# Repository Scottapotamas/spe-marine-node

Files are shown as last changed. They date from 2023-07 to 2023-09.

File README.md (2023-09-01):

# Underwater Sensor Node with Single Pair Ethernet
Prototype project to build a underwater sensor node, powered by and communicating with the surface via Single Pair Ethernet (10BASE-T1L + 802.3cg Type E Class 10-12).

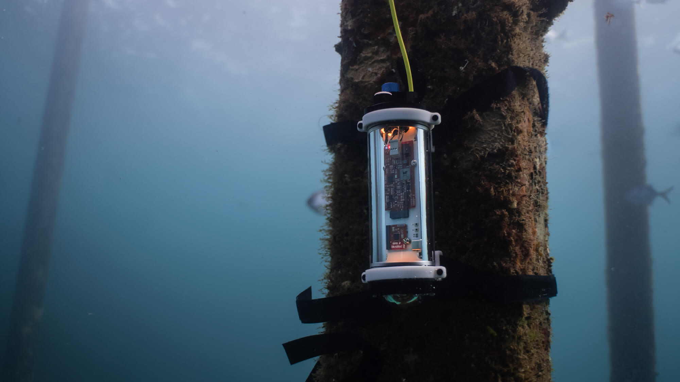
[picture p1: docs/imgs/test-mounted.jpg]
test-mounted


A more detailed write-up can be [read on Electric UI's blog](https://electricui.com/blog/spe-sensor-node).

# Mechanical

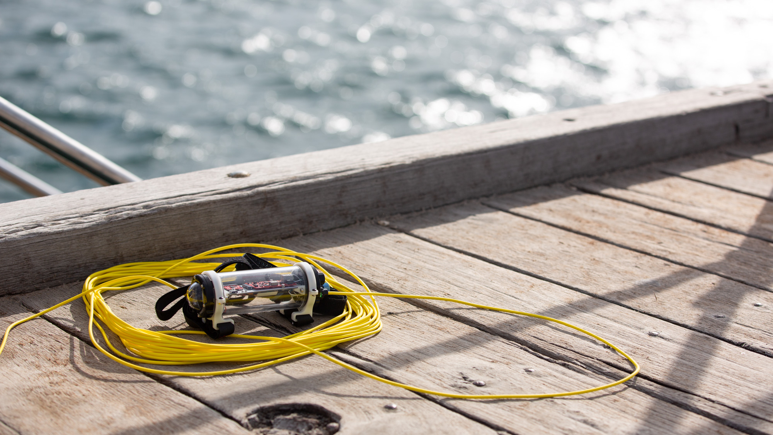
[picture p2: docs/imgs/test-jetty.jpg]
test-jetty


## Housing

The body of the sensor node is a 2″ acrylic tube (*~58mm OD*), with a pair of aluminium end-caps. This provides a working volume constrained by the 50 mm internal diameter and ~118 mm maximum gap between caps.

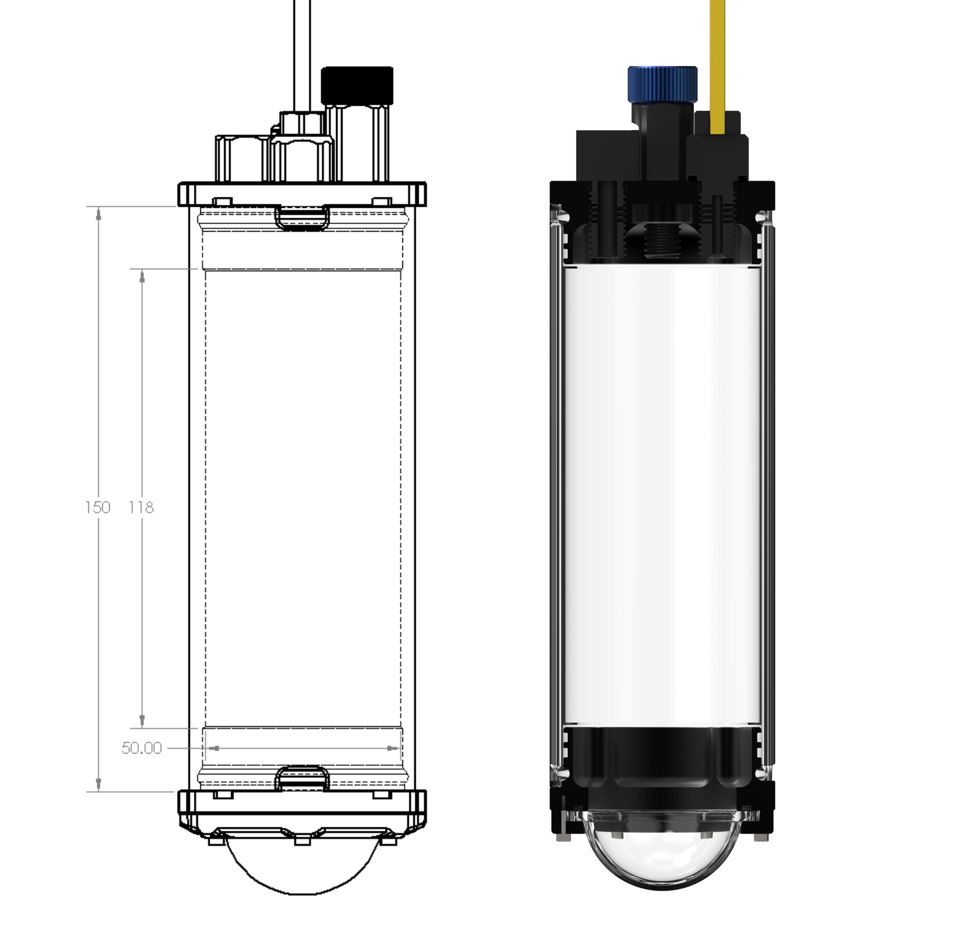
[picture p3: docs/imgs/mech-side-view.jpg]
mech-side-view


The top cap/bulkhead has 4×M10 threaded holes for accessories as part of BlueRobotic's hardware ecosystem. The assembled prototype is fitted with:

- 4.5mm Wetlink penetrator for the tether cable
- 10m rated pressure sensor
- White indicator LED
- Pressure relief/test valve

Whilst this prototype won't see properly deep water, this tube arrangement should be capable of  200m operation, and far deeper if an aluminium sleeve is used.

CAD models and assemblies are in `/mechanical/tube/`. Off-the-shelf parts are in `/mechanical/tube/cots/`.

## Internal brackets

A pair of 3D printed board mounts use the 4×M3 internal mounting holes in the bulkheads.

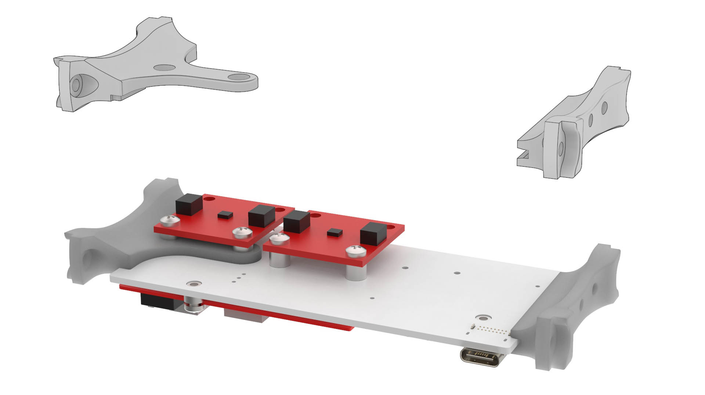
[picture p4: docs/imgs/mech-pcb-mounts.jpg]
mech-pcb-mounts


CAD models and STL files are in `/mechanical/tube/`. 

## Mounting

The tube itself doesn't have any features for mounting, so a pair of custom tube clamps were printed with the general goal of providing generic strap or wire mounting points. 

Files are in `/mechanical/mount/`.

# Electronics

Compatibility with the [Sparkfun MicroMod ecosystem](https://www.sparkfun.com/micromod) has been maintained where possible - building off of [Sparkfun's ADIN1110 function board](https://www.sparkfun.com/products/19038) for bring-up and early software tests.

PCB's were designed with KiCAD 7. Project files, gerbers and schematic PDF's are in `/electronics/`.

A small collection of calculator spreadsheets were made to help during the design process - these are in `/docs` and use Open Office `.ods` format.

Version 1.0 boards do have some minor issues which were tweaked during bench testing, so I'd recommend reviewing things thorough before copying anything into your designs.

## Backplane

Acting as the MicroMod 'carrier', providing the processor and function board connections, as well as regulation, I2C headers, and breakout pads for spare/conflicted IO. It also serves as the mounting interface for sensor payloads and custom hardware. 

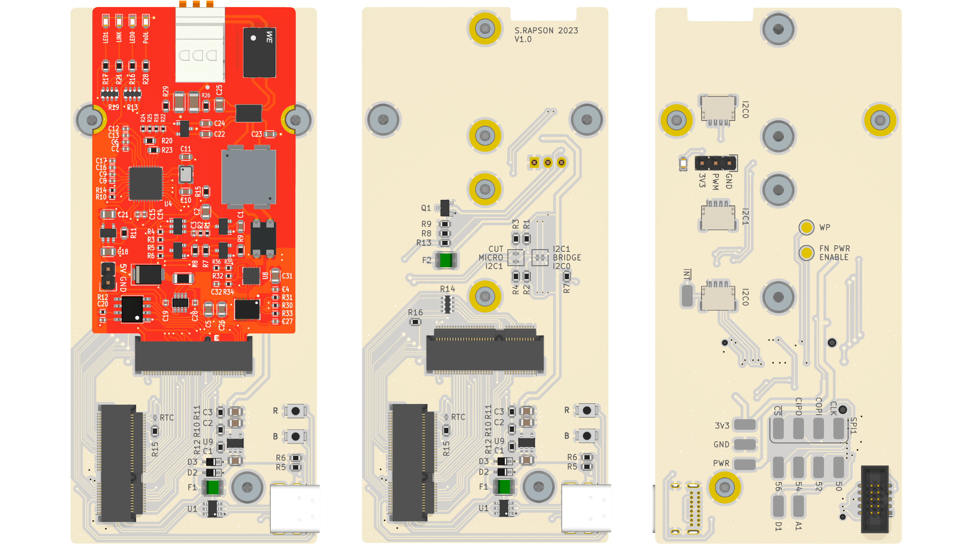
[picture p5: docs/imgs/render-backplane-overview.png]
render-backplane-overview


It's a 46×100 mm 1.6 mm 2-layer board with pretty relaxed fabrication requirements. 

## PD and PSE Function Boards

Both boards implement the ADIN1110 SPE transceiver in a similar manner to Sparkfun's function board, but exist as two variants which improve over the dev-kit by adding:

- Circuitry to act as a Class 10-12 PoDL **power supply** aka PSE (pictured below on left).

- VID circuitry to signal compliance as a Class 10-12 PoDL **powered device** aka PD (pictured on right).

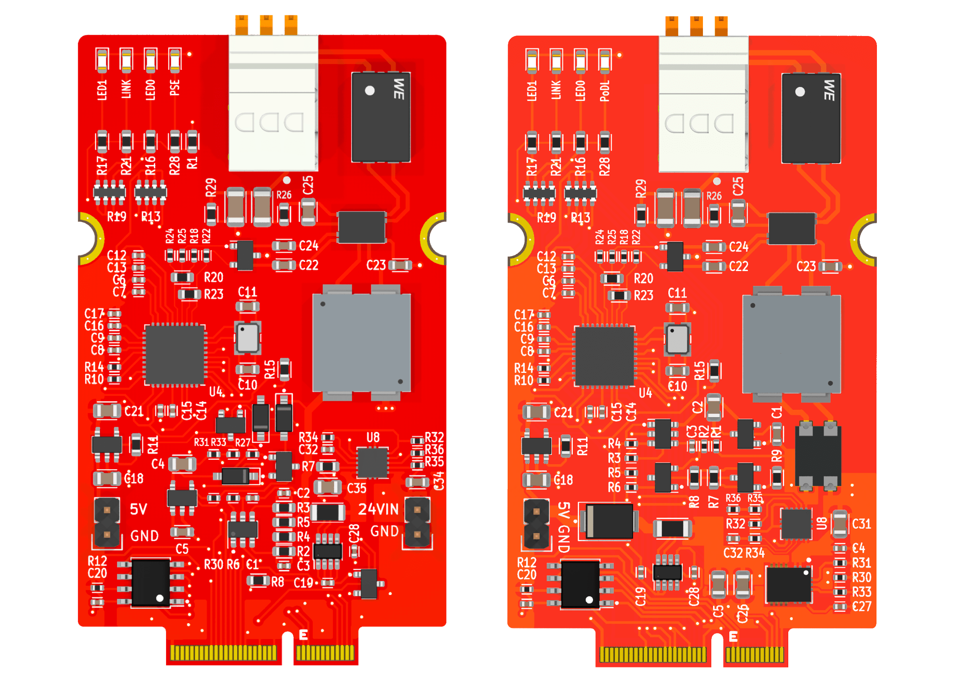
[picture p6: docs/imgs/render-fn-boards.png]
render-fn-boards
  

> These boards only provide detection, not classification via SCCP, and as such runs in 'fast-start mode'.

The PCB's are A×B mm, 0.8mm thick, 2-layer boards which can be manufactured with commodity fabs. I just used the raw straight PCB edge-connector without issues, but for best practice and/or frequent insertion cycles the edge-connector should be bevelled.

The blog post describes PoDL circuit behaviour and integration in more detail.

## Sensors

The project was designed without assuming any specific sensors would be used, but I used these I2C sensors:

- Temperature & Humidity - `SHTC3` via [Sparkfun `SEN-16467`](https://www.sparkfun.com/products/16467)
- Motion - `LSM6DSO` via [Sparkfun `SEN-18020`](https://www.sparkfun.com/products/18020)
- Depth/Pressure - `MS5837` via [BlueRobotics `Bar02`](https://bluerobotics.com/store/sensors-cameras/sensors/bar02-sensor-r1-rp/)

# Firmware

I used an ESP32 MicroMod processor board along with the Arduino toolchain. As such, there are external dependencies on the ESP32 Arduino core, [`electricui-embedded`](https://github.com/electricui/electricui-embedded), and Sparkfun packages for their [ESP32 boards](https://github.com/sparkfun/Arduino_Boards), [`LSM6DS0`](https://github.com/sparkfun/SparkFun_Qwiic_6DoF_LSM6DSO), [`SHTC3`](https://github.com/sparkfun/SparkFun_SHTC3_Arduino_Library) and [`ADIN1110`](https://github.com/sparkfun/SparkFun_ADIN1110_Arduino_Library) libraries.

I also depend on my own [`MS5837`](https://github.com/Scottapotamas/MS5837) library (external to this repo) for working with the pressure sensor.

The `/firmware` folder has some of the test-sketches written during testing:

- `spe-pse-io` - Bench-test PoDL PSE behaviour with a simple state-machine
- `lsm6ds0-fifo-test` - Configures and reads IMU samples periodically from the buffer
- `led-io-test` - Rough test using Pololu's APA102 library to check the 2×24 LED rings
- `spe-eui-bridge` - Transparent proxy of `electricui-embedded` packets with ADIN1110 raw buffers to serial ports.

> These sketches weren't written to act as examples or as reference material, and should be treated accordingly.

The main firmware is actually rather straightforward, running a superloop which runs each sub-system at a defined rate. Sub-systems never block, and are generally only responsible for their own behaviour. 

> **TODO: Cleanup and merge branches/sources into this repo**

# User Interface

> **TODO: Cleanup and merge sources into this repo**

The user interface is built with [Electric UI](https://electricui.com), and can be built and run by invoking `arc start` from `/interface`.

It handles visualisation of data streaming off the sensor node, and provides additional statistics and logging.

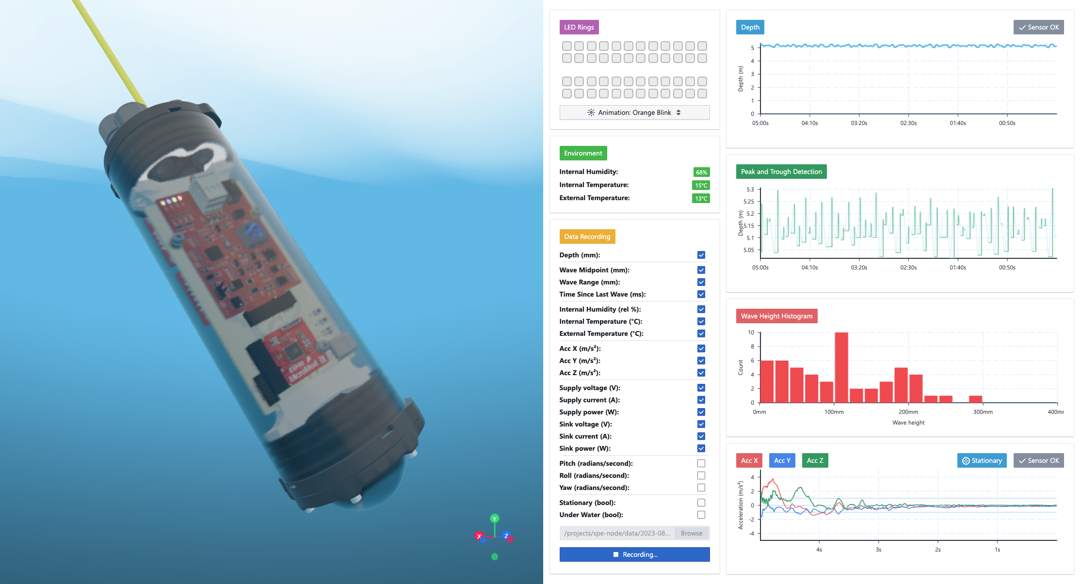
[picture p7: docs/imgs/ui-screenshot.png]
ui-screenshot


**TODO: Write part 2 post on data processing and visualisation**

# Additional Notes

_If_ you're planning on replicating this project, or part of it, some additional points of interest:

- I'm happy to answer questions or help with design changes to suit your ocean research project.
  - I'm also generally open to consulting work!
- Firmware is pretty specific to my own tooling and relies on external libraries for sensors and the Arduino ESP32 core.
- Read over BlueRobotics's guides for Wetlink penetrator use, enclosure assembly, pressure testing.
  - Definitely do remember to lubricate o-rings and the tube bulkheads as you slide them into the cylinder. It's _very difficult_ to get them out dry... 
- The tube *as designed and pictured* is positively buoyant and might need additional ballast weight depending on your application and safety requirements around handling.

Its also worth mentioning that the entire detailed conceptualisation, design, ordering, assembly, testing and writeup occurred in August 2023. There were many late nights, and as a result some design choices were made with simplicity or time-frame in mind.

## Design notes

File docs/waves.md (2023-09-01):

# Wave Height Monitoring Pipeline

These notes were internal thoughts/concepts during the project design phase, and have been kept for posterity.

___

Pressure sensor provides depth with `0.16 mBar` resolution when used in `8192` mode which would take ~16ms of ADC oversampling.

The actual design sample rate doesn't need to be this fast, but we might get better results by taking a faster stream of data and performing filtering manually.

## Test Data

I've not found any high-rate data for actual wave heights, only long-term observations in papers/online weather websites.

Testing the visualisations can likely be done with a series of superimposed signals:

- Low frequency sine to represent tidal changes
- Medium frequency, amplitude modulated sine to represent waves
- Some reasonably high frequency, low amplitude noise
- Gaussian/white noise + quantisation effects due to sensor behaviour and data processing

## Filtering

The raw signal should be filtered to retrieve as much of the original sine wave as possible, allowing for more accurate processing in later steps.

To start with, implementing the leaky integrator or a rolling median would probably work fine?

## Detecting waves

We want to know the height and wavelength/period.

To do this:

- Run a long-running average to provide baseline depth measurement.
- Perform min/max feature extraction to find the peaks and troughs of the waves.
  - Will likely need a debounce/timeout duration to handle noise
  - Ignore values within a deadband of the baseline depth, as 'very small' waves won't be reliable.
- With peak/trough event pairs, calculate the height of each wave.
- With peak event pairs, calculate the duration between them.
- Push height + period into a new datasource of waves

## Wave classification

With wave height and frequency data, we can then calculate some typical stats that meteorologists use/provide.

Information sourced from http://www.bom.gov.au/marine/knowledge-centre/reference/waves.shtml

We could attempt to classify waves into three types:

- Most frequent waves - about half the height of a significant wave
- Significant waves - about 14% of waves should be higher than these
- Maximum wave - about twice the height of significant waves. Expect 2-3 a day.

We could also render the sea-state value as per table:

| **Description** | **Height (metres)** | **Effect** | **WMO Sea State code** |
| --- | --- | --- | --- |
| Calm (glassy) | 0 | No waves breaking on beach | 0 |
| Calm (rippled)  | 0 - 0.1 | No waves breaking on beach | 1 |
| Smooth | 0.1 - 0.5 | Slight waves breaking on beach | 2 |
| Slight | 0.5 - 1.25 | Waves rock buoys and small craft | 3 |
| Moderate | 1.25 - 2.5 | Sea becoming furrowed | 4 |
| Rough | 2.5 - 4 | Sea deeply furrowed | 5 |
| Very rough | 4-6 | Sea much disturbed with rollers having steep fronts | 6 |
| High | 6-9 | Sea much disturbed with rollers having steep fronts (damage to foreshore) | 7 |

> Not sure what kind of time period to evaluate for sea-state values.
>
> Probably do a rolling X minute scan of the wave data and take the Yth percentile of heights?

## Visualisations

- Should attempt a realtime scrolling visualisation of wave height
  - Peak and trough detections annotated in real-time
  - Possibly horizontal/vertical annotations showing height and period?
  - Significant waves get a different colour or extra annotation?
  - Maximum waves get a different colour and annotation?

- Bar-chart comparing the height of each wave against the other as they are detected?
- Chart showing timing information for waves?
- Line-chart showing significant wave height and maximum wave height trends
  - Long-term data seems to be presented in like this https://www.qld.gov.au/environment/coasts-waterways/beach/monitoring/waves-sites/townsville

- Text display of sea-state code and description
- Text display of sea temperature

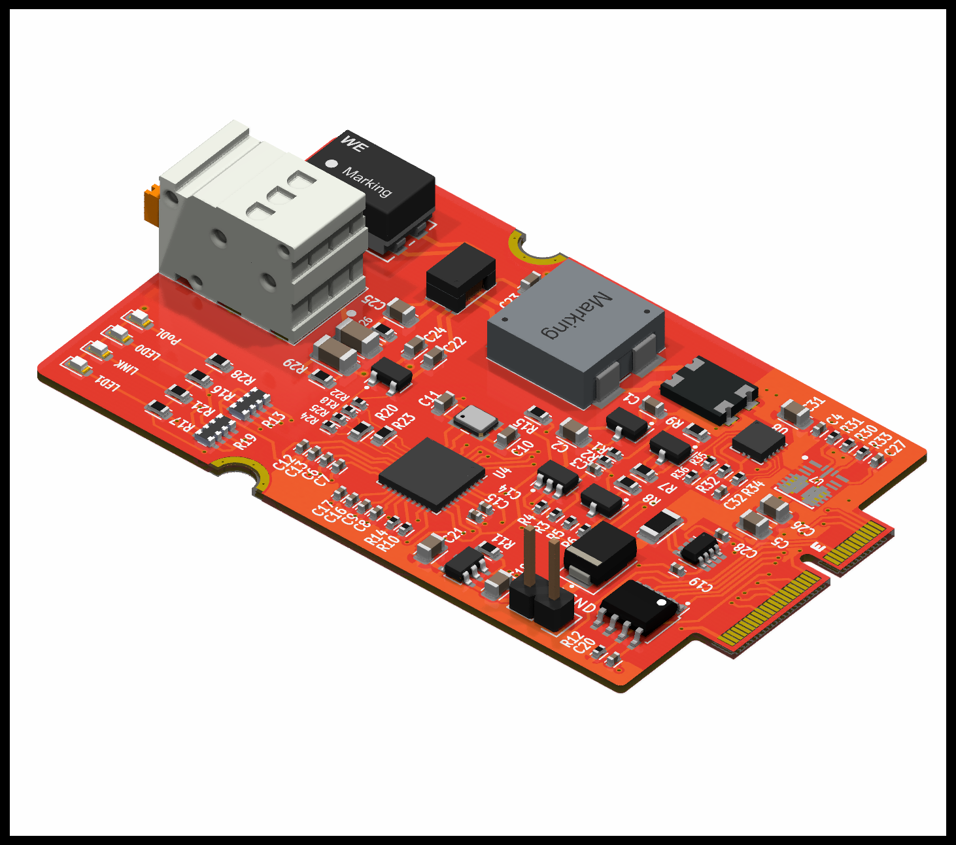
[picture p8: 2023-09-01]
docs/imgs/spe-sink.png

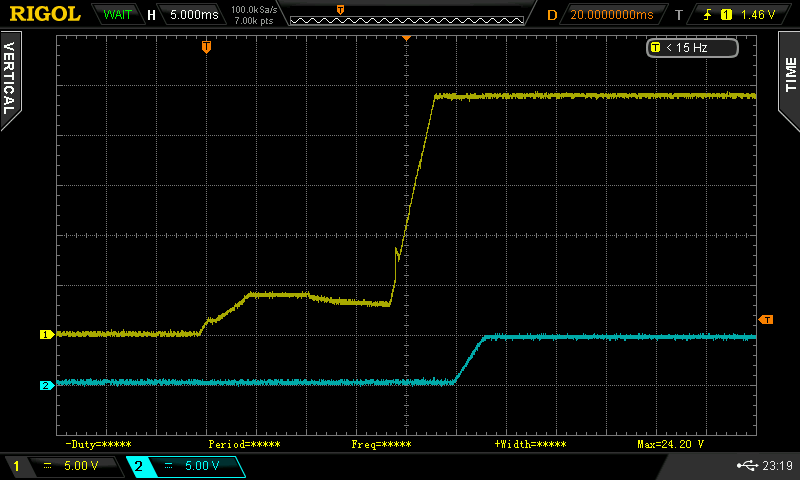
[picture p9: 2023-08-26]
docs/traces/pd-detection.png

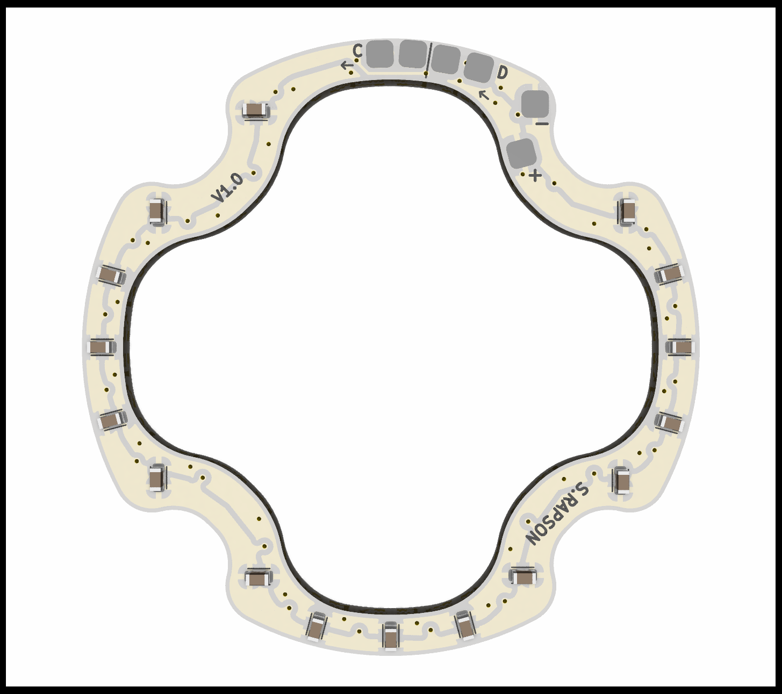
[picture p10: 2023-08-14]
docs/interior-lighting-back.png

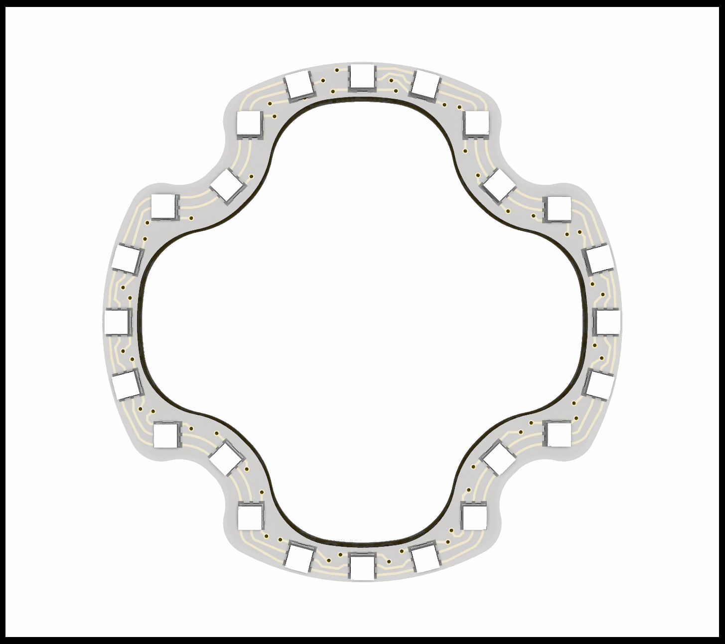
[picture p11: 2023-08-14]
docs/interior-lighting-front.png

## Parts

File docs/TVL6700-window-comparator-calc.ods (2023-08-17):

TLV6700 Window Comparator Calculations
V_IT+ | 0.4 | V
Low Threshold | 4.05 | V
High Threshold | 4.7 | V
Divider Current | 10 | uA | 0.00001 | A
Calculated Resistor Values
R Total | 4.70E+05 | Ohms | 470 | k
R3 | 40000 | Ohms | 40 | k
R2 | 6419.75308641975 | Ohms | 6.41975308641975 | k
R1 | 423580.24691358 | Ohms | 423.58024691358 | k
Actual Resistor Values
R3 | 39000 | Ohms | 39 | k
R2 | 15000 | Ohms | 15 | k
R1 | 390000 | Ohms | 390 | k
 |  |  |  |  | 444
Actual low threshold | 3.28888888888889 | V
Actual high threshold | 4.55384615384615 | V

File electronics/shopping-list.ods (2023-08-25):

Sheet: spe-sink
Reference | Qty | Value | Footprint | DNP | manf# | Supplier Part No | Board
R5 | 1 | 0R_1005M | Applidyne_Resistor:RESC1005X40N |  | CRCW04020000Z0ED | 1469661 | sink
R8 | 1 | 0R_1608M | Applidyne_Resistor:RESC1608X50N |  | MC0063W06030R | 9331662 | pse
R12 | 1 | 100K_1005M | Applidyne_Resistor:RESC1005X40N |  | ERJ2RKF1003X | 2302839 | sink
R12, R31 | 2 | 100K_1005M | Applidyne_Resistor:RESC1005X40N |  | ERJ2RKF1003X | 2302839 | pse
R7 | 1 | 100K_1608M | Applidyne_Resistor:RESC1608X50N |  | MC0063W06035100K | 9331719 | pse
C4, C6, C8, C12, C14, C16, C19, C20 | 8 | 100n_X7R_1005M | Applidyne_Capacitor:CAPC1005X60N |  | CGA2B3X7R1H104K050BB | 2210822 | sink
C1, C6, C8, C12, C14, C16, C19, C20 | 8 | 100n_X7R_1005M | Applidyne_Capacitor:CAPC1005X60N |  | CGA2B3X7R1H104K050BB | 2210822 | pse
C23 | 1 | 100n_X7R_1608M | Applidyne_Capacitor:CAPC1608X90N |  | C0603C104K5RACAUTO | 2070398 | sink
C23 | 1 | 100n_X7R_1608M | Applidyne_Capacitor:CAPC1608X90N |  | C0603C104K5RACAUTO | 2070398 | pse
R26 | 1 | 100R_1608M | Applidyne_Resistor:RESC1608X50N |  | MC0063W06035100R | 9331689 | sink
R26 | 1 | 100R_1608M | Applidyne_Resistor:RESC1608X50N |  | MC0063W06035100R | 9331689 | pse
R5 | 1 | 107K_1608M | Applidyne_Resistor:RESC1608X50N |  | ERJ-3EKF1073V | P107KHCT-ND | pse
R3, R6, R30 | 3 | 10K0_1005M | Applidyne_Resistor:RESC1005X40N |  | CRCW040210K0FKED | 1469669 | sink
R27, R30 | 2 | 10K0_1005M | Applidyne_Resistor:RESC1005X40N |  | CRCW040210K0FKED | 1469669 | pse
R11 | 1 | 10K0_1608M | Applidyne_Resistor:RESC1608X50N |  | CRGH0603F10K | 2332016 | sink
R1, R2, R3, R11 | 4 | 10K0_1608M | Applidyne_Resistor:RESC1608X50N |  | CRGH0603F10K | 2332016 | pse
R20, R23 | 2 | 10K2_1608M | Applidyne_Resistor:RESC1608X50N |  | RC0603FR-0710K2L | 311-10.2KHRCT-ND | sink
R20, R23 | 2 | 10K2_1608M | Applidyne_Resistor:RESC1608X50N |  | RC0603FR-0710K2L | 311-10.2KHRCT-ND | pse
C13, C15, C17, C32 | 4 | 10n_X7R_1005M | Applidyne_Capacitor:CAPC1005X60N |  | C0402C103K5RACTU | 1414575 | sink
C13, C15, C17, C32 | 4 | 10n_X7R_1005M | Applidyne_Capacitor:CAPC1005X60N |  | C0402C103K5RACTU | 1414575 | pse
R33 | 1 | 10R_1005M | Applidyne_Resistor:RESC1005X40N |  | CRCW040210R0FKED | 1652742 | pse
C31 | 1 | 10u_X5R_2012M_50V | Applidyne_Capacitor:CAPC2012X110N |  | GRM21BR61H106ME43L | 490-18664-1-ND | sink
C35 | 1 | 10u_X5R_2012M_50V | Applidyne_Capacitor:CAPC2012X110N |  | GRM21BR61H106ME43L | 490-18664-1-ND | pse
C2, C18, C21 | 3 | 10u_X7R_2012M | Applidyne_Capacitor:CAPC2012X110N |  | MC0805B106K6R3CT | 2320851 | sink
C4, C18, C21 | 3 | 10u_X7R_2012M | Applidyne_Capacitor:CAPC2012X110N |  | MC0805B106K6R3CT | 2320851 | pse
R34 | 1 | 13K_1005M | Applidyne_Resistor:RESC1005X40N |  | RC0402FR-0713KL | 311-13.0KLRCT-ND | sink
R34 | 1 | 13K_1005M | Applidyne_Resistor:RESC1005X40N |  | RC0402FR-0713KL | 311-13.0KLRCT-ND | pse
R31 | 1 | 15K_1005M | Applidyne_Resistor:RESC1005X40N |  | ERJ2RKF1502X | 2302754 | sink
D8 | 1 | 16V_500mW_SOD123 | Applidyne_SOD:SOD3715X145N |  | MMSZ5246B-7-F | MMSZ5246B-FDICT-ND | pse
R16, R21, R28 | 3 | 1K00_1608M | Applidyne_Resistor:RESC1608X50N |  | MCHP03W8F1001T5E | 1576283 | sink
R16, R21, R28 | 3 | 1K00_1608M | Applidyne_Resistor:RESC1608X50N |  | MCHP03W8F1001T5E | 1576283 | pse
R10, R14 | 2 | 1K5_1005M | Applidyne_Resistor:RESC1005X40N |  | CRCW04021K50FKED | 1653201 | sink
R10, R14 | 2 | 1K5_1005M | Applidyne_Resistor:RESC1005X40N |  | CRCW04021K50FKED | 1653201 | pse
R1 | 1 | 1M_1005M | Applidyne_Resistor:RESC1005X40N |  | CRCW04021M00FKED | 1469667 | sink
R29 | 1 | 1M_1608M | Applidyne_Resistor:RESC1608X50N |  | CRCW06031M00FKEA | 1469746 | sink
R29 | 1 | 1M_1608M | Applidyne_Resistor:RESC1608X50N |  | CRCW06031M00FKEA | 1469746 | pse
C28 | 1 | 1n_X7R_1005M | Applidyne_Capacitor:CAPC1005X60N |  | C0402C102K5RACTU | 1414573 | sink
C2, C3, C28 | 3 | 1n_X7R_1005M | Applidyne_Capacitor:CAPC1005X60N |  | C0402C102K5RACTU | 1414573 | pse
C29, C30 | 2 | 1n_X7R_3216M_2kV | Applidyne_Capacitor:CAPC3216X135N |  | KGM31AR73D102KU | 478-KGM31AR73D102KUCT-ND | sink
C29, C30 | 2 | 1n_X7R_3216M_2kV | Applidyne_Capacitor:CAPC3216X135N |  | KGM31AR73D102KU | 478-KGM31AR73D102KUCT-ND | pse
C7, C27 | 2 | 1u_X5R_1005M | Applidyne_Capacitor:CAPC1005X60N |  | C1005X5R1V105K050BC | 2346885 | sink
C7 | 1 | 1u_X5R_1005M | Applidyne_Capacitor:CAPC1005X60N |  | C1005X5R1V105K050BC | 2346885 | pse
C5, C34 | 2 | 1u_X7R_1608M | Applidyne_Capacitor:CAPC1608X90N |  | GRM188R61H105KAALD | 1845736 | pse
R8 | 1 | 20K0_1608M | Applidyne_Resistor:RESC1608X50N |  | CPF-A-0603B20KE1 | 2577005 | sink
C22, C24 | 2 | 220n_X7R_1608M | Applidyne_Capacitor:CAPC1608X90N |  | C1608X7R1C224K080AC | 2346897 | sink
C22, C24 | 2 | 220n_X7R_1608M | Applidyne_Capacitor:CAPC1608X90N |  | C1608X7R1C224K080AC | 2346897 | pse
C10, C11 | 2 | 22p_X7R_1608M | Applidyne_Capacitor:CAPC1608X90N |  | MC0603N220K500CT | 2309012 | sink
C10, C11 | 2 | 22p_X7R_1608M | Applidyne_Capacitor:CAPC1608X90N |  | MC0603N220K500CT | 2309012 | pse
R9 | 1 | 22R_1608M | Applidyne_Resistor:RESC1608X50N |  | MC0063W060314R22 | 2141539 | sink
C5, C26 | 2 | 22u_X5R_2012M | Applidyne_Capacitor:CAPC2012X110N |  | GRM21BR61E226ME44L | 1907510 | sink
R32 | 1 | 26K1_1005M | Applidyne_Resistor:RESC1005X40N |  | CRCW040226K1FKEDHP | 541-26.1KYCT-ND | sink
R32 | 1 | 26K1_1005M | Applidyne_Resistor:RESC1005X40N |  | CRCW040226K1FKEDHP | 541-26.1KYCT-ND | pse
R17 | 1 | 2K40_1608M | Applidyne_Resistor:RESC1608X50N |  | MC0063W060312K4 | 9330879 | sink
R17 | 1 | 2K40_1608M | Applidyne_Resistor:RESC1608X50N |  | MC0063W060312K4 | 9330879 | pse
Q1 | 1 | 2N7002P | Applidyne_SOT:SOT95P240X110-3L16N |  | 2N7002,215 | 436-7379 | sink
Q1 | 1 | 2N7002P | Applidyne_SOT:SOT95P240X110-3L16N |  | 2N7002,215 | 436-7379 | pse
C3 | 1 | 330p_X7R_1005M | Applidyne_Capacitor:CAPC1005X60N |  | GRM155R71H331KA01D | 2494212 | sink
R36 | 1 | 36K_1005M | Applidyne_Resistor:RESC1005X40N |  | ERA-2AEB363X | P36KDCCT-ND | sink
R36 | 1 | 36K_1005M | Applidyne_Resistor:RESC1005X40N |  | ERA-2AEB363X | P36KDCCT-ND | pse
R33 | 1 | 40K2_1005M | Applidyne_Resistor:RESC1005X40N |  | ERJ2RKF4022X | P40.2KLCT-ND | sink
R2, R4 | 2 | 470K_1005M | Applidyne_Resistor:RESC1005X40N |  | ERJ2GEJ474X | P470KJCT-ND | sink
C9 | 1 | 470n_X5R_1005M | Applidyne_Capacitor:CAPC1005X60N |  | GRM155R61A474KE15 | 1828863 | sink
C9 | 1 | 470n_X5R_1005M | Applidyne_Capacitor:CAPC1005X60N |  | GRM155R61A474KE15 | 1828863 | pse
C25 | 1 | 470n_X7R_2012M_100V | Applidyne_Capacitor:CAPC2012X110N |  | 08051C474K4T4A | 581-08051C474K4T4A | sink
C25 | 1 | 470n_X7R_2012M_100V | Applidyne_Capacitor:CAPC2012X110N |  | 08051C474K4T4A | 581-08051C474K4T4A | pse
R6 | 1 | 47K_1005M | Applidyne_Resistor:RESC1005X40N |  | RC0402FR-0747KL | 9239430 | pse
R22, R24 | 2 | 49R9_1005M | Applidyne_Resistor:RESC1005X40N |  | ERJ-2RKD49R9X | P15987CT-ND | sink
R22, R24 | 2 | 49R9_1005M | Applidyne_Resistor:RESC1005X40N |  | ERJ-2RKD49R9X | P15987CT-ND | pse
R15 | 1 | 4K7_1608M | Applidyne_Resistor:RESC1608X50N |  | MC0063W060354K7 | 9332154 | sink
R15 | 1 | 4K7_1608M | Applidyne_Resistor:RESC1608X50N |  | MC0063W060354K7 | 9332154 | pse
R13, R19 | 2 | 4K7_QUAD_ARRAY_1608M | Applidyne_Resistor:R_Array_Concave_4x1608M |  | EXB38V472JV | 2060105RL | sink
R13, R19 | 2 | 4K7_QUAD_ARRAY_1608M | Applidyne_Resistor:R_Array_Concave_4x1608M |  | EXB38V472JV | 2060105RL | pse
C1 | 1 | 56n_X7R_1608M | Applidyne_Capacitor:CAPC1608X90N |  | C0603C563K5RACTU | 1865538 | sink
R18, R25 | 2 | 5K1_1005M | Applidyne_Resistor:RESC1005X40N |  | CRCW04025K10FKED | 541-5.10KLCT-ND | sink
R18, R25 | 2 | 5K1_1005M | Applidyne_Resistor:RESC1005X40N |  | CRCW04025K10FKED | 541-5.10KLCT-ND | pse
R35 | 1 | 680K_1005M | Applidyne_Resistor:RESC1005X40N |  | RC0402FR-07680KL | YAG3211CT-ND | sink
R35 | 1 | 680K_1005M | Applidyne_Resistor:RESC1005X40N |  | RC0402FR-07680KL | YAG3211CT-ND | pse
D6 | 1 | 6V2_500mW_SOD123 | Applidyne_SOD:SOD3715X145N |  | MMSZ5234B-7-F | 2306178 | pse
R4 | 1 | 91K_1608M | Applidyne_Resistor:RESC1608X50N |  | ERJPA3F9102V | 2335960RL | pse
R7 | 1 | 9K09_1608M | Applidyne_Resistor:RESC1608X50N |  | MCWF06W9091BTL | 2339315 | sink
U4 | 1 | ADIN1110 | Applidyne_QFN:QFN50P600X600X100-40T350X350N |  | ADIN1110BCPZ-R7 | 505-ADIN1110BCPZ-R7CT-ND | sink
U4 | 1 | ADIN1110 | Applidyne_QFN:QFN50P600X600X100-40T350X350N |  | ADIN1110BCPZ-R7 | 505-ADIN1110BCPZ-R7CT-ND | pse
U6 | 1 | AP2112K-3.3 | Applidyne_SOT:SOT95P280X145-5L30N |  | AP2112K-3.3TRG1 | 621-AP2112K-3.3TRG1 | sink
U6 | 1 | AP2112K-3.3 | Applidyne_SOT:SOT95P280X145-5L30N |  | AP2112K-3.3TRG1 | 621-AP2112K-3.3TRG1 | pse
U1 | 1 | AP7375-33 | Applidyne_SOT:SOT95P240X110-3L16N |  | AP7375-33SA-7 | 31-AP7375-33SA-7CT-ND | sink
IC1 | 1 | AT24C02C-SSHM | Applidyne_SOIC:SOIC127P600X330-8L2N |  | AT24C02C-SSHM | 1971995 | sink
IC1 | 1 | AT24C02C-SSHM | Applidyne_SOIC:SOIC127P600X330-8L2N |  | AT24C02C-SSHM | 1971995 | pse
U3 | 1 | ATL431LIB | Applidyne_SOT:SOT95P240X110-3L16N |  | ATL431LIBIDBZR | 296-53203-1-ND | sink
D6 | 1 | B240Q-13-F | Applidyne_SOD:SODFL5436X262N |  | B240Q-13-F | B240Q-13-FDICT-ND | sink
D4 | 1 | BAV99 | Applidyne_SOT:SOT95P240X110-3L16N |  | BAV99 | 544-4534 | pse
D4 | 1 | CD-HD2006L | Applidyne_Device:CD-HD2x(L) |  | CD-HD2006L | 118-CD-HD2006LCT-ND | sink
L3 | 1 | COMM_MODE_1000uH_800mA_0.3R | Applidyne_Inductor:WE-SL2 |  | 744222 | 732-1485-1-ND | sink
L3 | 1 | COMM_MODE_1000uH_800mA_0.3R | Applidyne_Inductor:WE-SL2 |  | 744222 | 732-1485-1-ND | pse
P2 | 1 | CONN_01X02 | Applidyne_Connector_Wurth:61300211121 |  | 61300211121 | 2356153 | sink
P1, P2 | 2 | CONN_01X02 | Applidyne_Connector_Wurth:61300211121 |  | 61300211121 | 2356153 | pse
J1 | 1 | CONN_01X05_RA | Applidyne_Connector:CUI_TBL009-254-03 |  | TBL009-254-03GY-2GY | 102-TBL009-254-03GY-2GY-ND | sink
J1 | 1 | CONN_01X05_RA | Applidyne_Connector:CUI_TBL009-254-03 |  | TBL009-254-03GY-2GY | 102-TBL009-254-03GY-2GY-ND | pse
L2 | 1 | COUPLED_47uH_1500mA_340mOhm | Applidyne_Inductor:WE-MCRI-1040 |  | 7448991470 | 732-13378-1-ND | sink
L2 | 1 | COUPLED_47uH_1500mA_340mOhm | Applidyne_Inductor:WE-MCRI-1040 |  | 7448991470 | 732-13378-1-ND | pse
D7 | 1 | D1213A | Applidyne_SOT:SOT95P240X110-3L16N |  | D1213A-02SOL-7 | D1213A-02SOL-7DICT-ND | sink
D7 | 1 | D1213A | Applidyne_SOT:SOT95P240X110-3L16N |  | D1213A-02SOL-7 | D1213A-02SOL-7DICT-ND | pse
Q2 | 1 | DMP6350SQ | Applidyne_SOT:SOT95P240X110-3L16N |  | DMP6350SQ-7 | 621-DMP6350SQ-7 | pse
U5 | 1 | INA186A3 | Applidyne_SOT:SOT23-8P65_280X145L45X30N |  | INA186A3IDDFR | 296-INA186A3IDDFRCT-ND | sink
U2 | 1 | INA186A3 | Applidyne_SOT:SOT23-8P65_280X145L45X30N |  | INA186A3IDDFR | 296-INA186A3IDDFRCT-ND | pse
D3 | 1 | LED_BLUE_1608M | Applidyne_LED:LEDC1608X80L40N |  | 5988091107F | 350-2037-1-ND | sink
D3 | 1 | LED_BLUE_1608M | Applidyne_LED:LEDC1608X80L40N |  | 5988091107F | 350-2037-1-ND | pse
D1 | 1 | LED_GREEN_1608M | Applidyne_LED:LEDC1608X80L40N |  | 5988070107F | 1465991 | sink
D1 | 1 | LED_GREEN_1608M | Applidyne_LED:LEDC1608X80L40N |  | 5988070107F | 1465991 | pse
D5 | 1 | LED_RED_1608M | Applidyne_LED:LEDC1608X80L40N |  | 5988010107F | 1465988 | sink
D5 | 1 | LED_RED_1608M | Applidyne_LED:LEDC1608X80L40N |  | 5988010107F | 1465988 | pse
D2 | 1 | LED_YELLOW_1608M | Applidyne_LED:LEDC1608X80L40N |  | 5988040107F | 1465989 | sink
D2 | 1 | LED_YELLOW_1608M | Applidyne_LED:LEDC1608X80L40N |  | 5988040107F | 1465989 | pse
U2 | 1 | MCP65R41T | Applidyne_SOT:SOT95P240X110-6L16N |  | MCP65R41T-1202E/CHY |  | sink
X2 | 1 | MICROMOD_FUNCTION_BOARD_EDGE | Applidyne_Connector:M.2-MICROMOD-FN-CARD-EDGE |  |  |  | sink
X2 | 1 | MICROMOD_FUNCTION_BOARD_EDGE | Applidyne_Connector:M.2-MICROMOD-FN-CARD-EDGE
U3 | 1 | NSI50010YT1G | Applidyne_SOD:SOD3715X145N |  | NSI50010YT1G | NSI50010YT1GOSCT-ND | pse
TEST1 | 1 | PROBE_PAD | Applidyne_Test:TP200 |  | N/A |  | sink
R27 | 1 | R01_3216M | Applidyne_Resistor:RESC3216X60N |  | WSLP1206R0100FEA | 683-6215 | sink
R9 | 1 | R05_3216M | Applidyne_Resistor:RESC3216X60L |  | WSLP1206R0500FEA | 683-6215 | pse
X1 | 1 | RH100-25.000-13-F-0715 | Applidyne_Crystal:OSCCC320X250X60L90X100N |  | RH100-25.000-13-F-0715-EXT-TR-NS1 | 2151-RH100-25.000-13-F-0715-EXT-TR-NS1CT-ND | sink
X1 | 1 | RH100-25.000-13-F-0715 | Applidyne_Crystal:OSCCC320X250X60L90X100N |  | RH100-25.000-13-F-0715-EXT-TR-NS1 | 2151-RH100-25.000-13-F-0715-EXT-TR-NS1CT-ND | pse
U5 | 1 | S-1212-7V | Applidyne_SOT:SOT95P280X145-5L30N |  | S-1212B70-M5T1U | 1662-2787-1-ND | pse
SL2, SL3, SL4, SL5, SL6, SL7 | 6 | SOLDER-LINK-2-TINY | Applidyne_Link:SJ1005-2N |  | ManufacturerPartNo | SupplierPartNo | sink
SL2, SL3, SL4, SL5, SL6, SL7 | 6 | SOLDER-LINK-2-TINY | Applidyne_Link:SJ1005-2N |  | ManufacturerPartNo | SupplierPartNo | pse
U1 | 1 | TLV6700 | Applidyne_SOT:SOT95P280X145-6L50N |  | TLV6700DDCR |  | pse
U7 | 1 | TLVM23625RDNR | Applidyne_QFN:QFN50P450X350X200-11-FCMOD11 |  | TLVM23625RDNR | 296-TLVM23625RDNRCT-ND | sink
U8 | 1 | TPS26625 | Applidyne_SON:SON50P300X300X90-11T240X165N_RELIEF |  | TPS26625DRCR | 296-52606-1-ND | sink
U8 | 1 | TPS26625 | Applidyne_SON:SON50P300X300X90-11T240X165N_RELIEF |  | TPS26625DRCR | 296-52606-1-ND | pse
L1 | 1 | WE-STST_74930000 | Applidyne_Inductor:WE-STST |  | 74930000 | 732-74930000CT-ND | sink
L1 | 1 | WE-STST_74930000 | Applidyne_Inductor:WE-STST |  | 74930000 | 732-74930000CT-ND | pse

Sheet: Sheet3
Board | - all - |  |  | Ordered from Digikey
 |  |  |  | Part in sample books
Value | Supplier Part No | Sum - Qty
0R_1005M | 1469661 | 1
0R_1608M | 9331662 | 1
100K_1005M | 2302839 | 3
100K_1608M | 9331719 | 1
100n_X7R_1005M | 2210822 | 16
100n_X7R_1608M | 2070398 | 2
100R_1608M | 9331689 | 2
107K_1608M | P107KHCT-ND | 1
10K0_1005M | 1469669 | 5
10K0_1608M | 2332016 | 5
10K2_1608M | 311-10.2KHRCT-ND | 4
10n_X7R_1005M | 1414575 | 8
10R_1005M | 1652742 | 1
10u_X5R_2012M_50V | 490-18664-1-ND | 2
10u_X7R_2012M | 2320851 | 6
13K_1005M | 311-13.0KLRCT-ND | 2
15K_1005M | 2302754 | 1
16V_500mW_SOD123 | MMSZ5246B-FDICT-ND | 1 | MBR0580S1-7
1K00_1608M | 1576283 | 6
1K5_1005M | 1653201 | 4
1M_1005M | 1469667 | 1
1M_1608M | 1469746 | 2
1n_X7R_1005M | 1414573 | 4
1n_X7R_3216M_2kV | 478-KGM31AR73D102KUCT-ND | 4
1u_X5R_1005M | 2346885 | 3
1u_X7R_1608M | 1845736 | 2
20K0_1608M | 2577005 | 1
220n_X7R_1608M | 2346897 | 4
22p_X7R_1608M | 2309012 | 4
22R_1608M | 2141539 | 1
22u_X5R_2012M | 1907510 | 2
26K1_1005M | 541-26.1KYCT-ND | 2
2K40_1608M | 9330879 | 2
2N7002P | 436-7379 | 2
330p_X7R_1005M | 2494212 | 1
36K_1005M | P36KDCCT-ND | 2
40K2_1005M | P40.2KLCT-ND | 1
470K_1005M | P470KJCT-ND | 2
470n_X5R_1005M | 1828863 | 2
470n_X7R_2012M_100V | 581-08051C474K4T4A | 2
47K_1005M | 9239430 | 1
49R9_1005M | P15987CT-ND | 4
4K7_1608M | 9332154 | 2
4K7_QUAD_ARRAY_1608M | 2060105RL | 4
56n_X7R_1608M | 1865538 | 1
5K1_1005M | 541-5.10KLCT-ND | 4
680K_1005M | YAG3211CT-ND | 2
6V2_500mW_SOD123 | 2306178 | 1 | MMSZ5232BT1G
91K_1608M | 2335960RL | 1
9K09_1608M | 2339315 | 1
ADIN1110 | 505-ADIN1110BCPZ-R7CT-ND | 2
AP2112K-3.3 | 621-AP2112K-3.3TRG1 | 2
AP7375-33 | 31-AP7375-33SA-7CT-ND | 1
AT24C02C-SSHM | 1971995 | 2
ATL431LIB | 296-53203-1-ND | 1
B240Q-13-F | B240Q-13-FDICT-ND | 1
BAV99 | 544-4534 | 1
CD-HD2006L | 118-CD-HD2006LCT-ND | 1
COMM_MODE_1000uH_800mA_0.3R | 732-1485-1-ND | 2
CONN_01X02 | 2356153 | 3
CONN_01X05_RA | 102-TBL009-254-03GY-2GY-ND | 2
COUPLED_47uH_1500mA_340mOhm | 732-13378-1-ND | 2
D1213A | D1213A-02SOL-7DICT-ND | 2
DMP6350SQ | 621-DMP6350SQ-7 | 1
INA186A3 | 296-INA186A3IDDFRCT-ND | 2
LED_BLUE_1608M | 350-2037-1-ND | 2
LED_GREEN_1608M | 1465991 | 2
LED_RED_1608M | 1465988 | 2
LED_YELLOW_1608M | 1465989 | 2
MCP65R41T | (empty) | 1
MICROMOD_FUNCTION_BOARD_EDGE | (empty) | 2
NSI50010YT1G | NSI50010YT1GOSCT-ND | 1
PROBE_PAD | (empty) | 1
R01_3216M | 683-6215 | 1
R05_3216M | 683-6215 | 1
RH100-25.000-13-F-0715 | 2151-RH100-25.000-13-F-0715-EXT-TR-NS1CT-ND | 2
S-1212-7V | 1662-2787-1-ND | 1
SOLDER-LINK-2-TINY | SupplierPartNo | 12
TLV6700 | (empty) | 1
TLVM23625RDNR | 296-TLVM23625RDNRCT-ND | 1
TPS26625 | 296-52606-1-ND | 2
WE-STST_74930000 | 732-74930000CT-ND | 2
Total Result |  | 198

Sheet: Pivot Table_spe-sink_1
Board | - all - |  |  | Ordered from Digikey
 |  |  |  | Part in sample books
Value | Supplier Part No | Sum - Qty
0R_1005M | 1469661 | 1
0R_1608M | 9331662 | 1
100K_1005M | 2302839 | 3
100K_1608M | 9331719 | 1
100n_X7R_1005M | 2210822 | 16
100n_X7R_1608M | 2070398 | 2
100R_1608M | 9331689 | 2
107K_1608M | P107KHCT-ND | 1
10K0_1005M | 1469669 | 5
10K0_1608M | 2332016 | 5
10K2_1608M | 311-10.2KHRCT-ND | 4
10n_X7R_1005M | 1414575 | 8
10R_1005M | 1652742 | 1
10u_X5R_2012M_50V | 490-18664-1-ND | 2
10u_X7R_2012M | 2320851 | 6
13K_1005M | 311-13.0KLRCT-ND | 2
15K_1005M | 2302754 | 1
16V_500mW_SOD123 | MMSZ5246B-FDICT-ND | 1 | MBR0580S1-7
1K00_1608M | 1576283 | 6
1K5_1005M | 1653201 | 4
1M_1005M | 1469667 | 1
1M_1608M | 1469746 | 2
1n_X7R_1005M | 1414573 | 4
1n_X7R_3216M_2kV | 478-KGM31AR73D102KUCT-ND | 4
1u_X5R_1005M | 2346885 | 3
1u_X7R_1608M | 1845736 | 2
20K0_1608M | 2577005 | 1
220n_X7R_1608M | 2346897 | 4
22p_X7R_1608M | 2309012 | 4
22R_1608M | 2141539 | 1
22u_X5R_2012M | 1907510 | 2
26K1_1005M | 541-26.1KYCT-ND | 2
2K40_1608M | 9330879 | 2
2N7002P | 436-7379 | 2
330p_X7R_1005M | 2494212 | 1
36K_1005M | P36KDCCT-ND | 2
40K2_1005M | P40.2KLCT-ND | 1
470K_1005M | P470KJCT-ND | 2
470n_X5R_1005M | 1828863 | 2
470n_X7R_2012M_100V | 581-08051C474K4T4A | 2
47K_1005M | 9239430 | 1
49R9_1005M | P15987CT-ND | 4
4K7_1608M | 9332154 | 2
4K7_QUAD_ARRAY_1608M | 2060105RL | 4
56n_X7R_1608M | 1865538 | 1
5K1_1005M | 541-5.10KLCT-ND | 4
680K_1005M | YAG3211CT-ND | 2
6V2_500mW_SOD123 | 2306178 | 1 | MMSZ5232BT1G
91K_1608M | 2335960RL | 1
9K09_1608M | 2339315 | 1
ADIN1110 | 505-ADIN1110BCPZ-R7CT-ND | 2
AP2112K-3.3 | 621-AP2112K-3.3TRG1 | 2
AP7375-33 | 31-AP7375-33SA-7CT-ND | 1
AT24C02C-SSHM | 1971995 | 2
ATL431LIB | 296-53203-1-ND | 1
B240Q-13-F | B240Q-13-FDICT-ND | 1
BAV99 | 544-4534 | 1
CD-HD2006L | 118-CD-HD2006LCT-ND | 1
COMM_MODE_1000uH_800mA_0.3R | 732-1485-1-ND | 2
CONN_01X02 | 2356153 | 3
CONN_01X05_RA | 102-TBL009-254-03GY-2GY-ND | 2
COUPLED_47uH_1500mA_340mOhm | 732-13378-1-ND | 2
D1213A | D1213A-02SOL-7DICT-ND | 2
DMP6350SQ | 621-DMP6350SQ-7 | 1
INA186A3 | 296-INA186A3IDDFRCT-ND | 2
LED_BLUE_1608M | 350-2037-1-ND | 2
LED_GREEN_1608M | 1465991 | 2
LED_RED_1608M | 1465988 | 2
LED_YELLOW_1608M | 1465989 | 2
MCP65R41T | (empty) | 1
MICROMOD_FUNCTION_BOARD_EDGE | (empty) | 2
NSI50010YT1G | NSI50010YT1GOSCT-ND | 1
PROBE_PAD | (empty) | 1
R01_3216M | 683-6215 | 1
R05_3216M | 683-6215 | 1
RH100-25.000-13-F-0715 | 2151-RH100-25.000-13-F-0715-EXT-TR-NS1CT-ND | 2
S-1212-7V | 1662-2787-1-ND | 1
SOLDER-LINK-2-TINY | SupplierPartNo | 12
TLV6700 | (empty) | 1
TLVM23625RDNR | 296-TLVM23625RDNRCT-ND | 1
TPS26625 | 296-52606-1-ND | 2
WE-STST_74930000 | 732-74930000CT-ND | 2
Total Result |  | 198

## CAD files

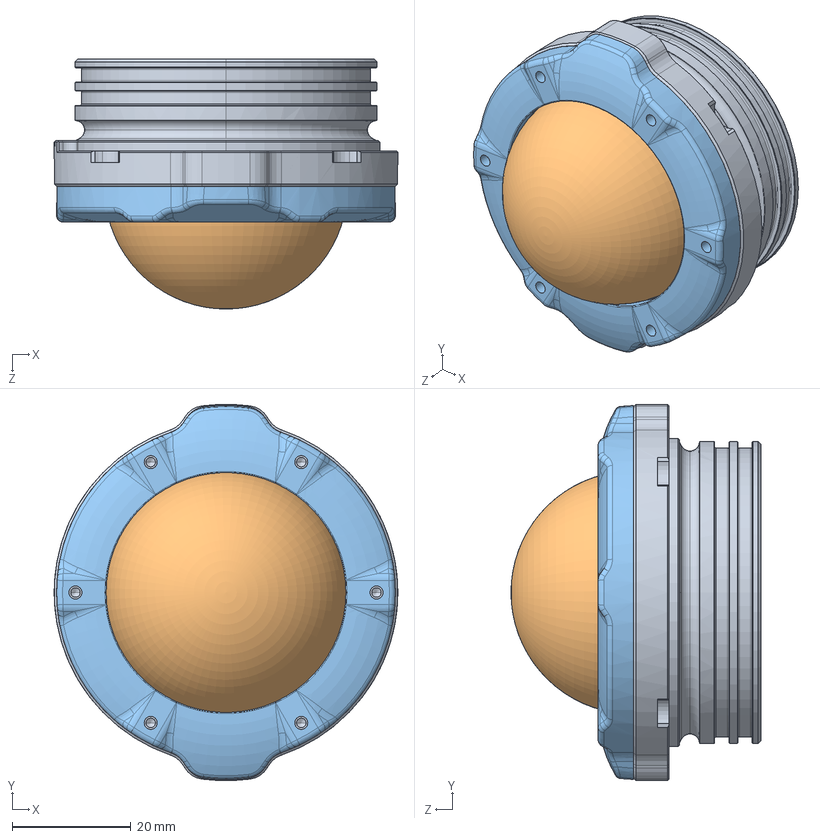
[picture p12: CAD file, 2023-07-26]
mechanical/tube/cap-dome.SLDASM
58.0 x 63.4 x 42.2 mm
WTE2-M-LOCKING-FLANGE-SEAL-R1
WTE2-P-DOME-R1
WTE2-P-RETAINING-RING-R1

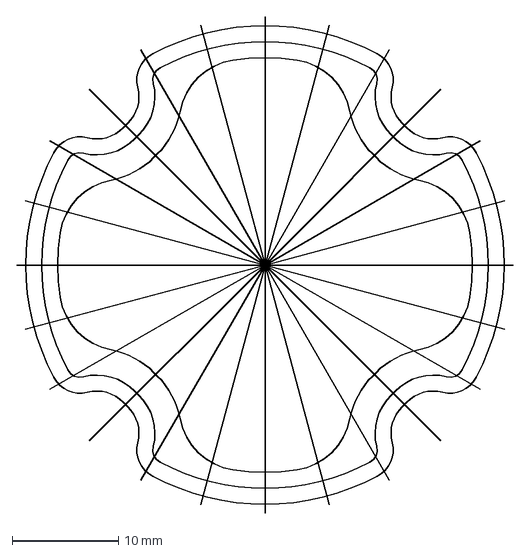
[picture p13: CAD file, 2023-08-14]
electronics/interior-lighting/flange-led-ring.DXF
46.8 x 46.8 mm

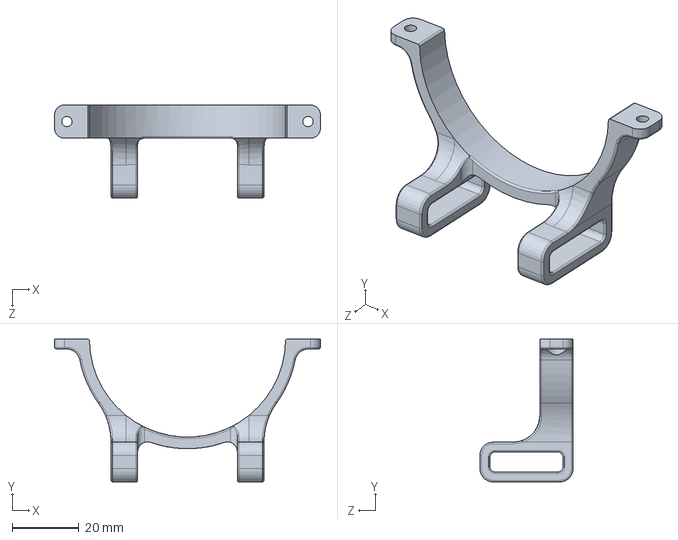
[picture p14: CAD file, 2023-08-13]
mechanical/mount/clamp-strap-lower.SLDPRT
80.0 x 43.0 x 28.0 mm

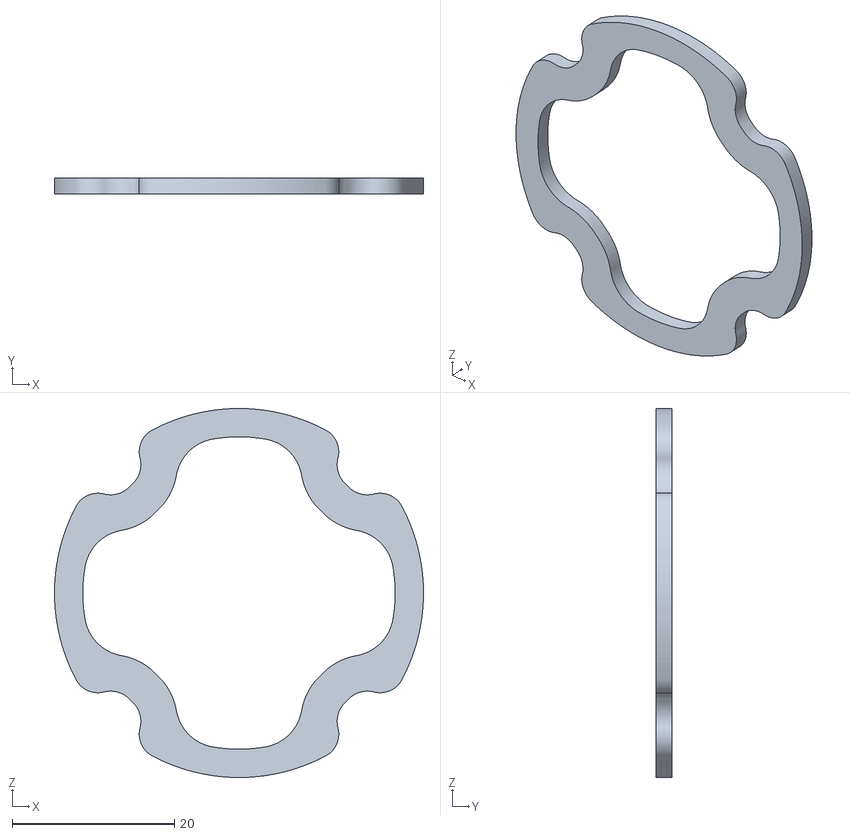
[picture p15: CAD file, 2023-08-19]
mechanical/tube/led-diffuser-2mm-thick.STL
45.5 x 2.00 x 45.5

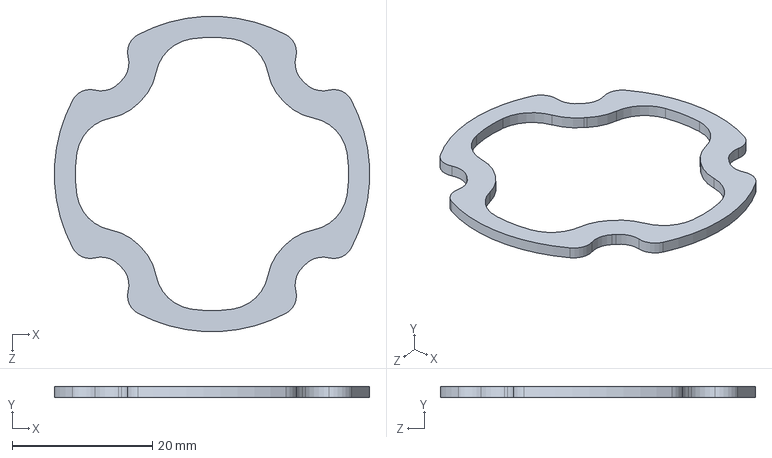
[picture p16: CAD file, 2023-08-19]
mechanical/tube/pcb-blanks/flange-led-ring.SLDPRT
44.9 x 1.60 x 44.9 mm

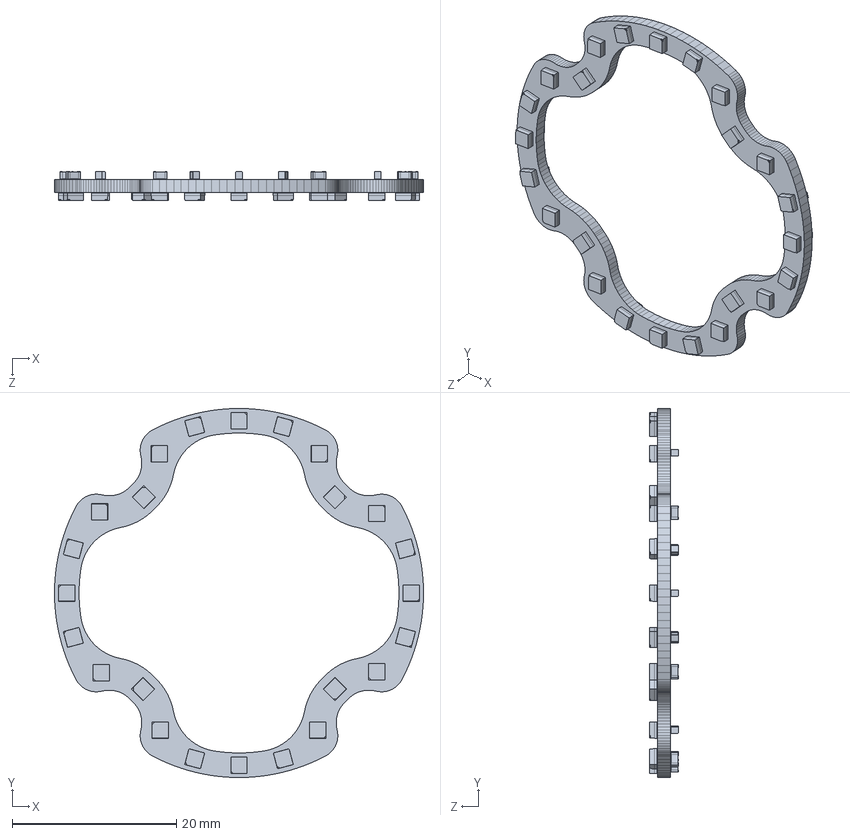
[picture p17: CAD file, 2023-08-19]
mechanical/tube/pcb-models/interior-lighting.SLDPRT
45.0 x 45.0 x 3.48 mm

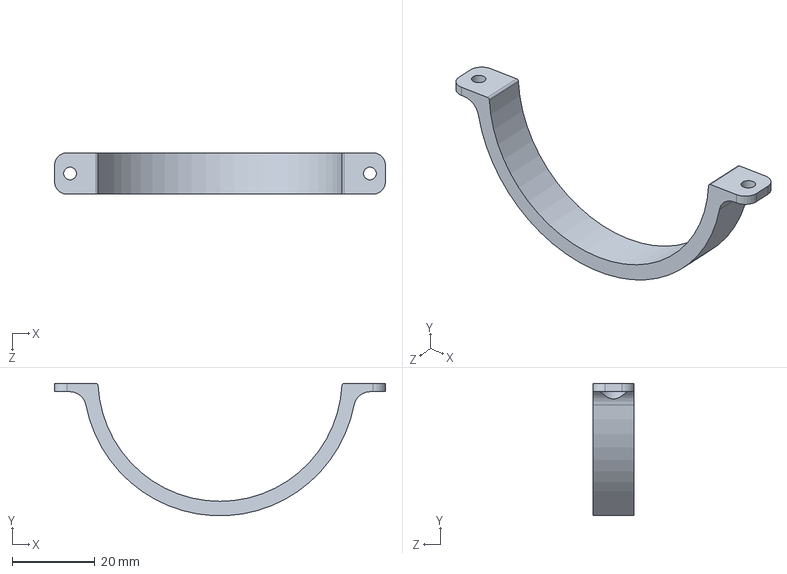
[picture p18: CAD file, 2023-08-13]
mechanical/mount/clamp-strap-upper.SLDPRT
80.0 x 31.9 x 10.0 mm

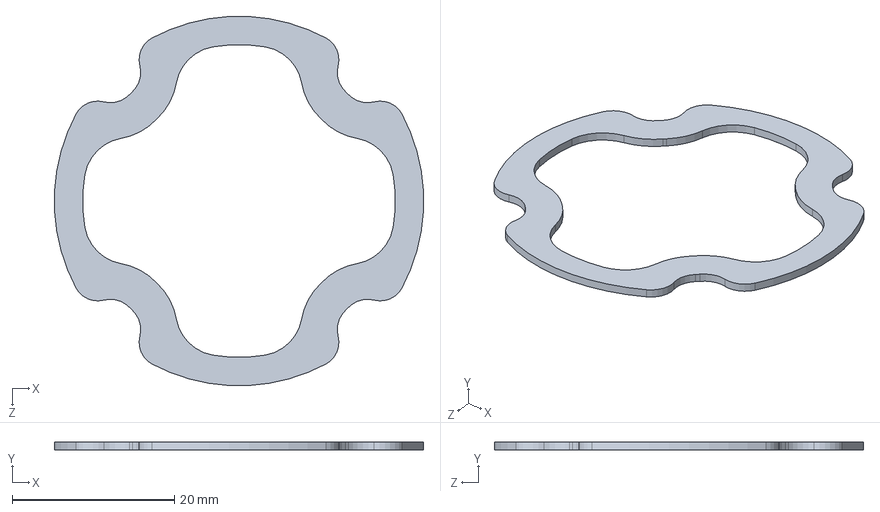
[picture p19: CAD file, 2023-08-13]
mechanical/tube/led-diffuser.SLDPRT
45.4 x 1.00 x 45.4 mm

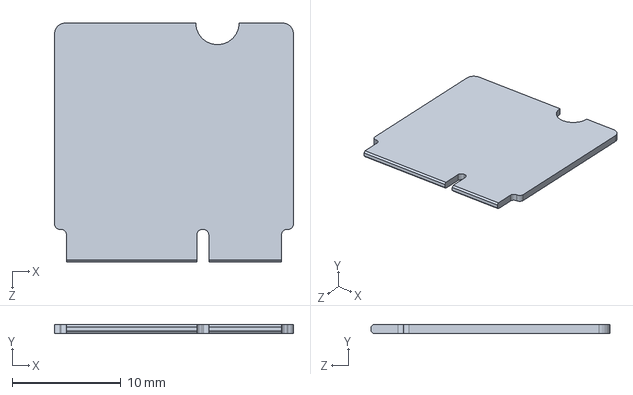
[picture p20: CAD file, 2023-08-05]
mechanical/tube/pcb-blanks/micro-mod-stub.SLDPRT
22.0 x 0.8 x 22.0 mm

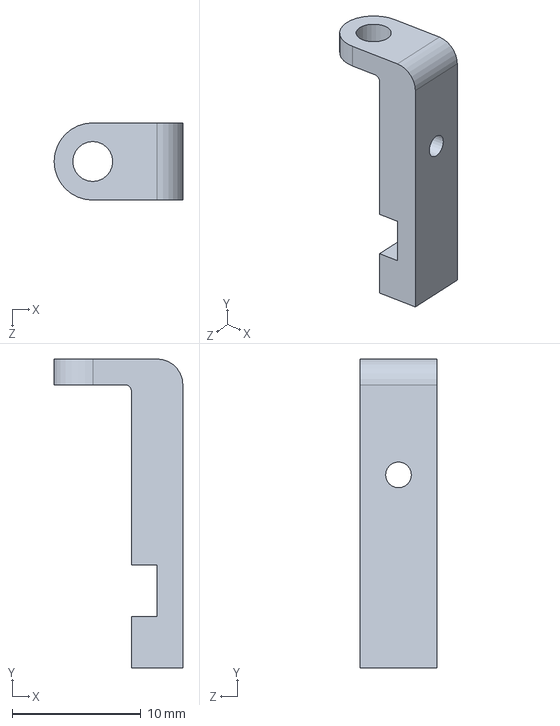
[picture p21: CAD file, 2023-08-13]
mechanical/mount/bulkhead-internal-mast.SLDPRT
10.0 x 24.0 x 6.00 mm

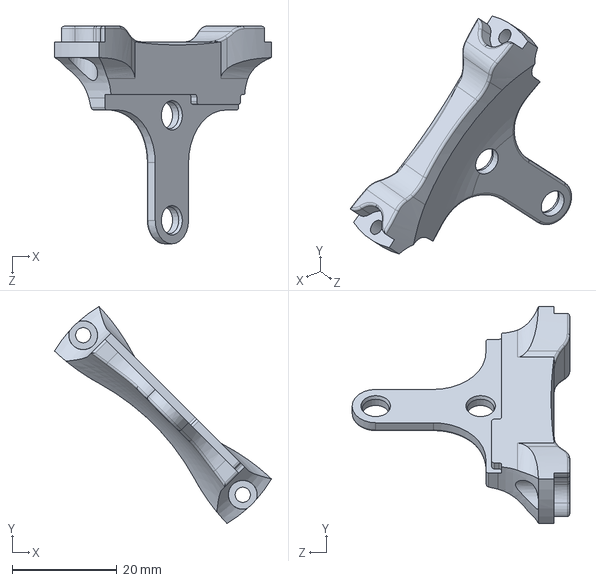
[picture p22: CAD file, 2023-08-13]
mechanical/tube/mounting-spine.SLDPRT
41.3 x 41.3 x 41.5 mm

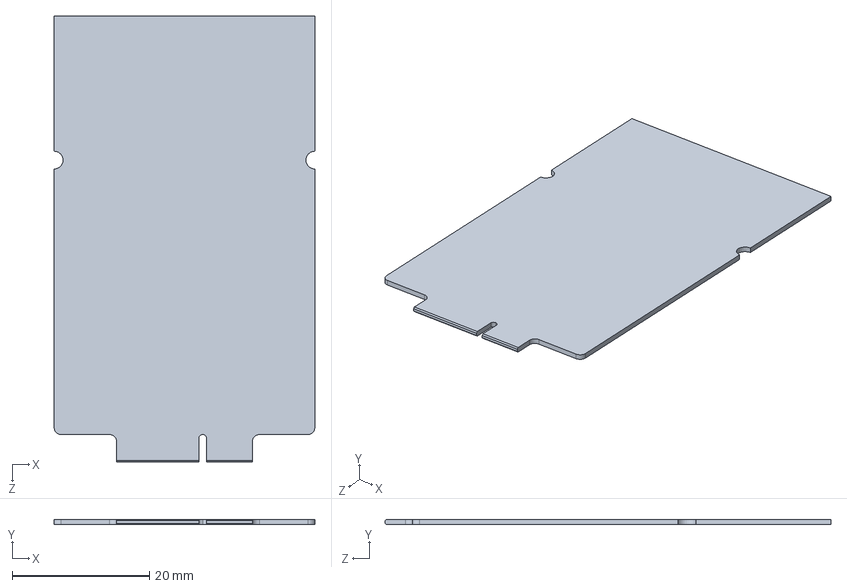
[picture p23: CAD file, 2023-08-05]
mechanical/tube/pcb-blanks/function-board-stub.SLDPRT
38.0 x 0.8 x 65.0 mm

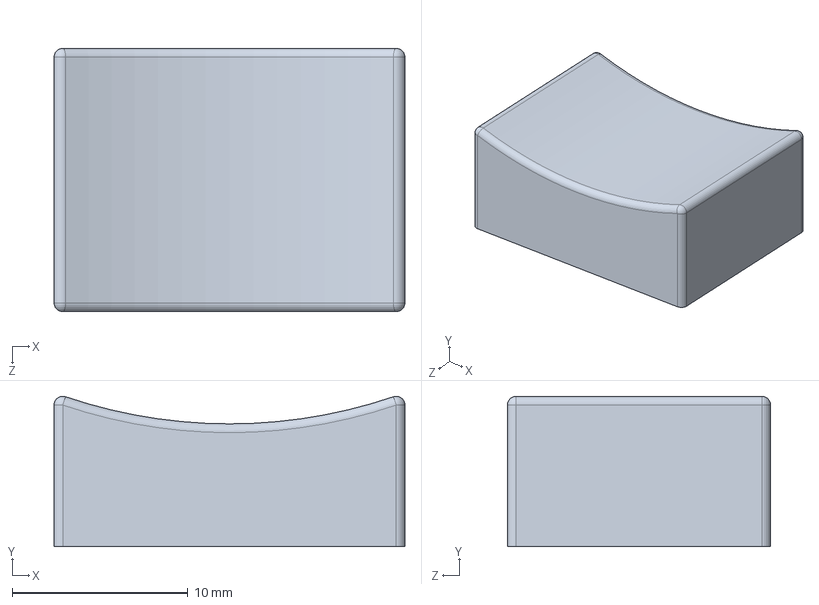
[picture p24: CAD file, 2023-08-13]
mechanical/mount/display-stand-small.SLDPRT
20.0 x 8.57 x 15.0 mm

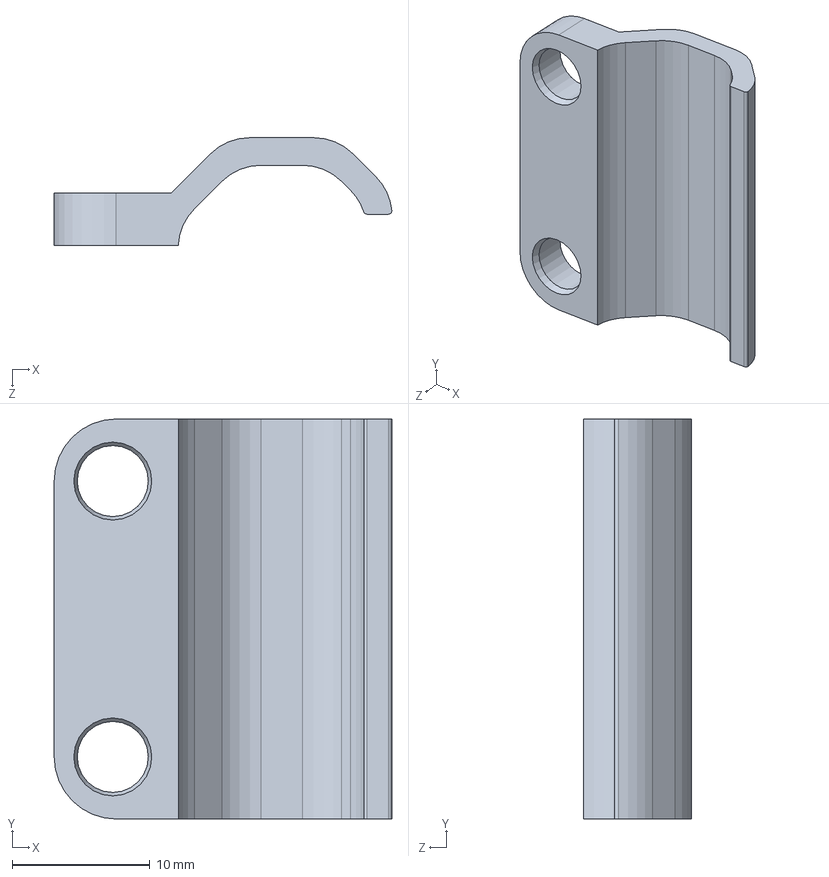
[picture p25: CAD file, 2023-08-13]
mechanical/tube/cable-tidy.SLDPRT
24.5 x 29.0 x 7.80 mm

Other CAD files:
mechanical/tube/pcb-blanks/sf-qwiic-sensor.SLDPRT
mechanical/tube/mounting-spine-lower.SLDPRT
mechanical/tube/cots/BAR02-ASM-R2-PUBLIC.SLDPRT
mechanical/tube/cots/PRV-M10-ASM-R1-RP.SLDPRT
mechanical/tube/cots/BALLAST-200G-R2.SLDPRT
mechanical/tube/cots/INDICATOR-M10-X-R2-PUBLIC.SLDPRT
mechanical/tube/cots/WLP-M10-4.5MM-PUBLIC.SLDPRT
mechanical/tube/cots/WTE2-M-LOCKING-FLANGE-CAP-4-HOLE-R1.SLDPRT
mechanical/tube/cots/WTE2-M-LOCKING-FLANGE-CAP-BLANK-R1.SLDPRT
mechanical/tube/cots/WTE2-M-LOCKING-FLANGE-SEAL-R1.SLDPRT
mechanical/tube/cots/WTE2-P-DOME-R1.SLDPRT
mechanical/tube/cots/WTE2-P-LOCKING-TUBE-150-R1.SLDPRT
mechanical/tube/cots/WTE2-P-RETAINING-RING-R1.SLDPRT
mechanical/tube/cots/fathom-utp-4mm-mockup.SLDPRT
mechanical/tube/fasteners/M2.5x4-pan-head.sldprt
mechanical/tube/fasteners/M2x10-screw.SLDPRT
mechanical/tube/led-diffuser.STL
mechanical/tube/mounting-spine-lower.STL
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

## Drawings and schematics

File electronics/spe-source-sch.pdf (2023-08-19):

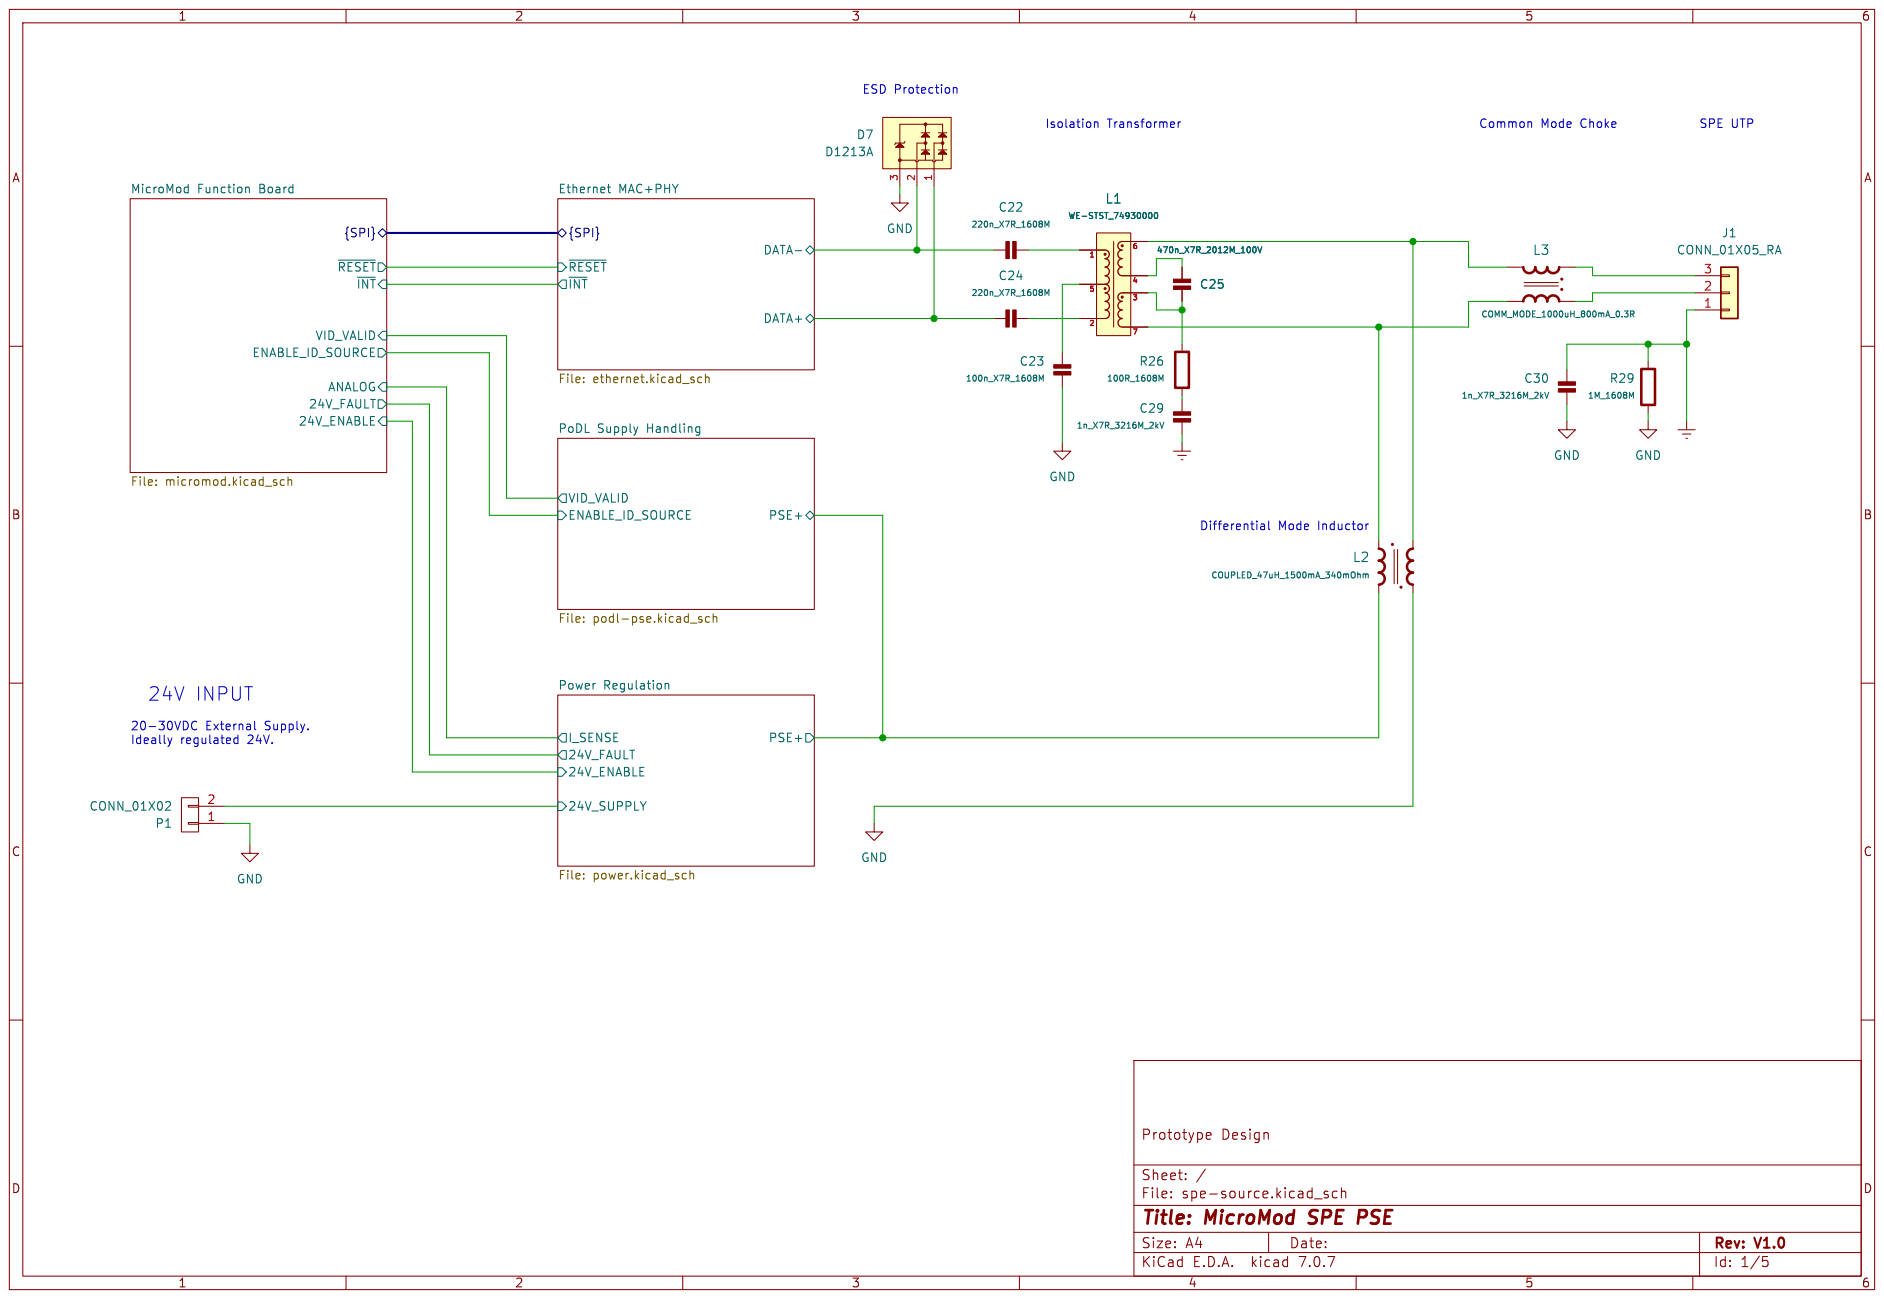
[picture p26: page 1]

~{RESET}
Power Regulation File: power.kicad_sch VID_VALID

Id: 1/5 Title: MicroMod SPE PSE

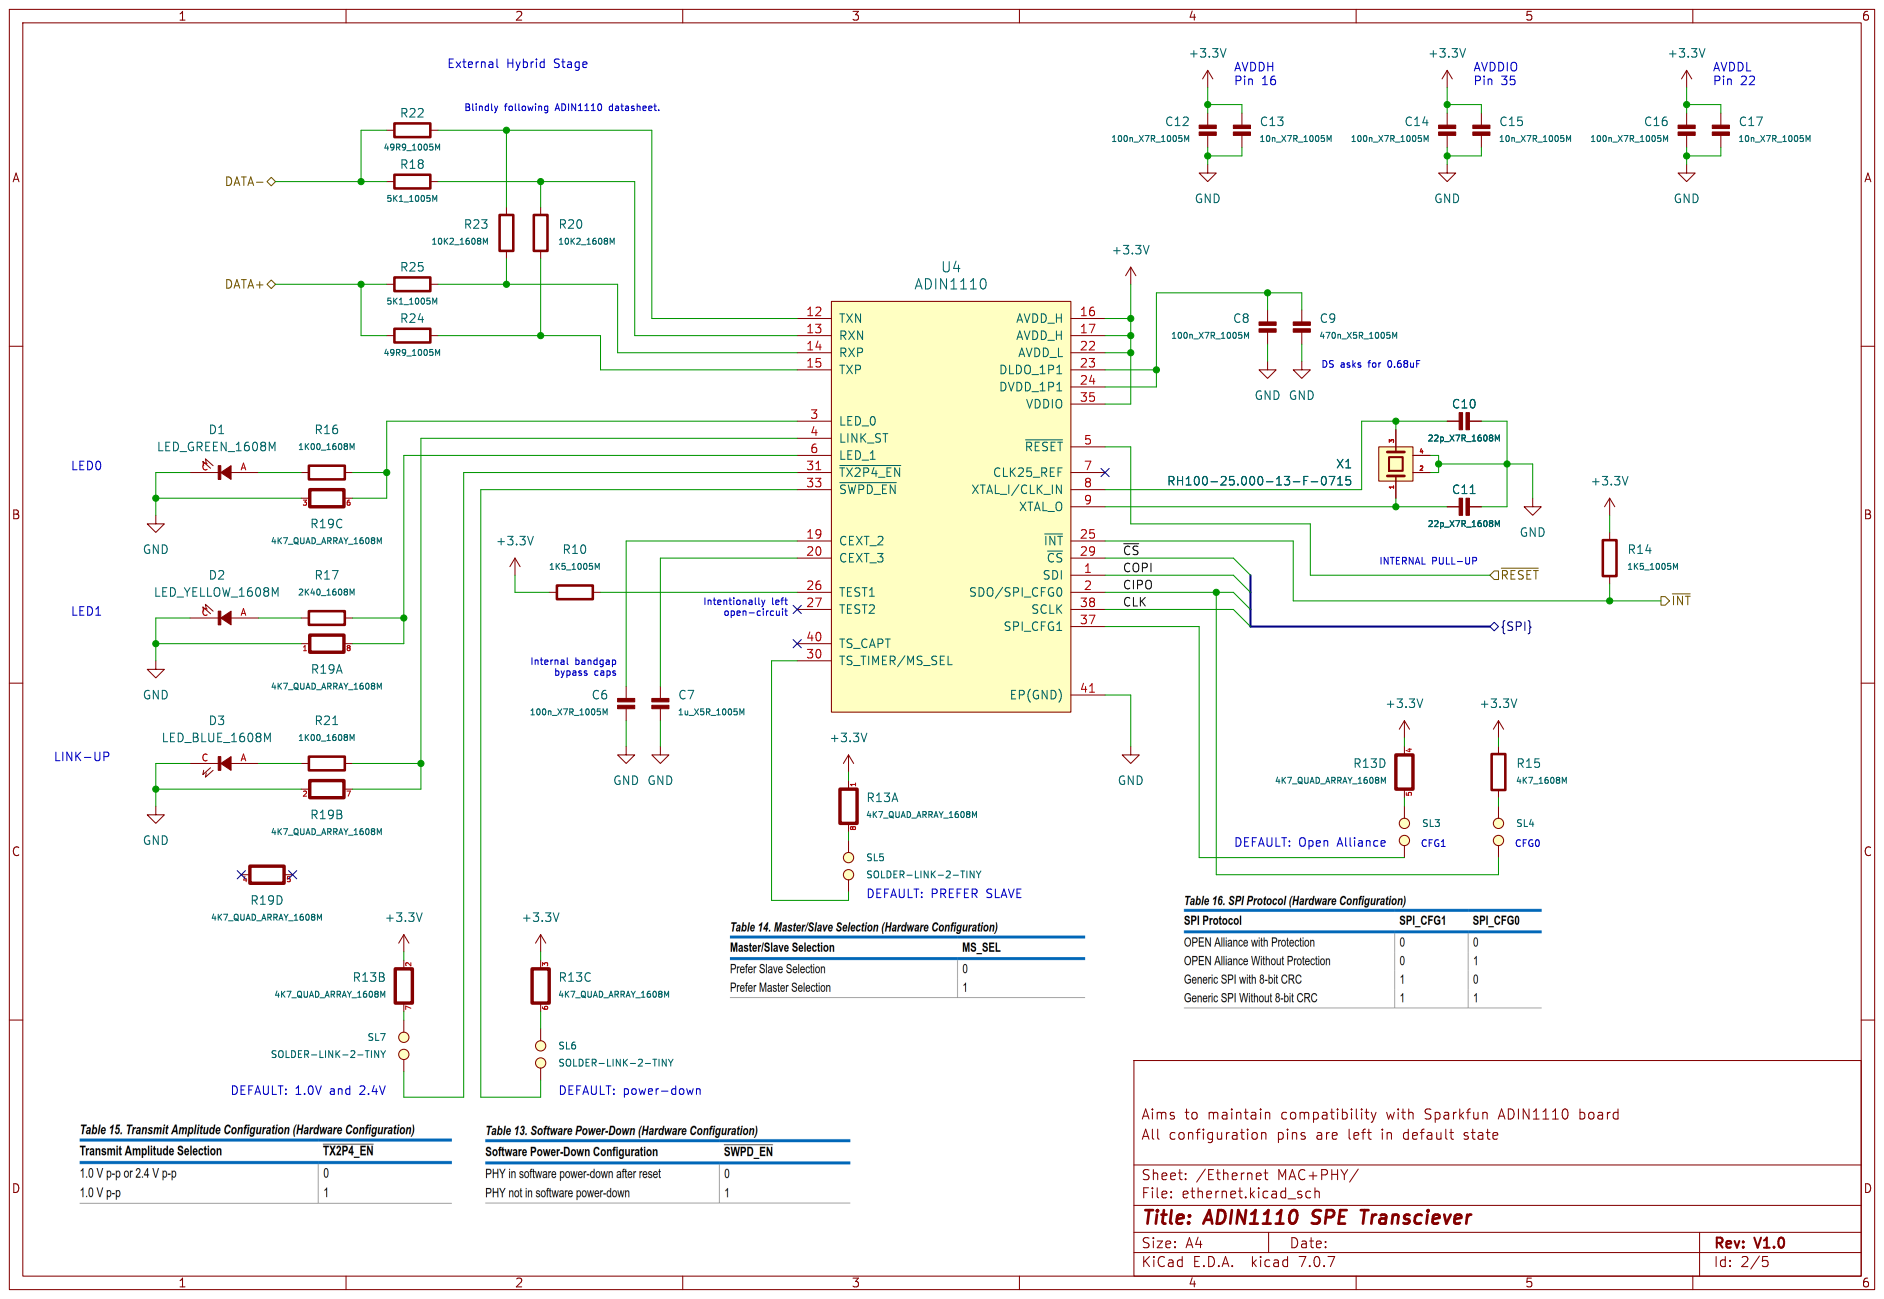
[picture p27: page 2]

Pin 35 DS asks for 0.68uF DEFAULT: Open Alliance DEFAULT: PREFER SLAVE

SL5 SOLDER-LINK-2-TINY +3.3V GND

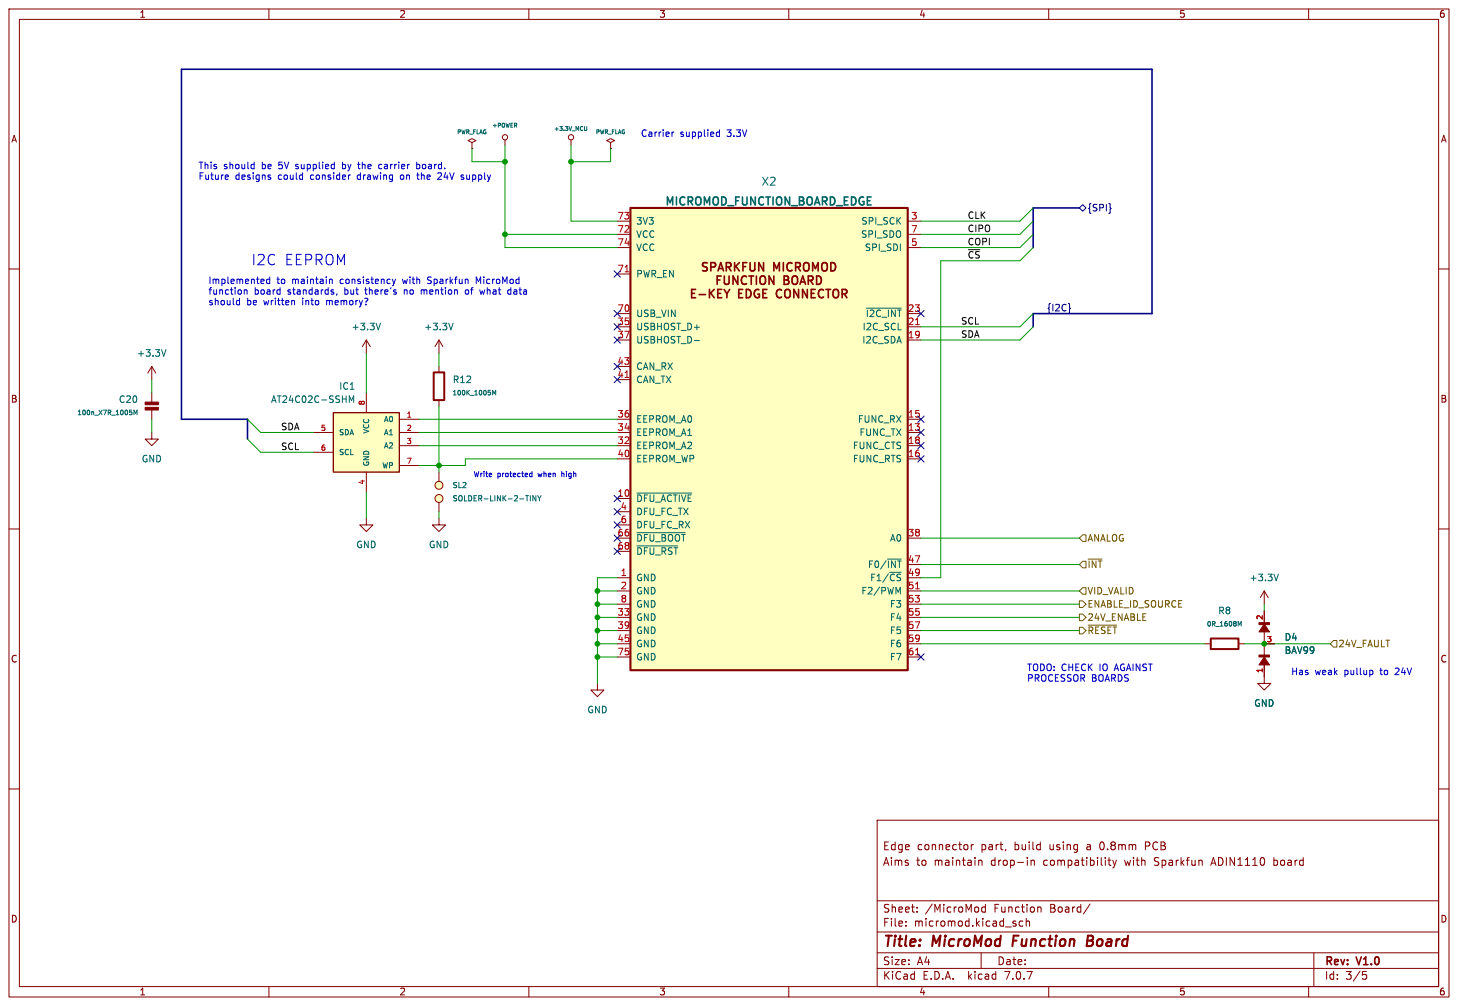
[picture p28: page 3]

4 SDA 5 SCL 6 WP 7 VCC

SL2 SOLDER-LINK-2-TINY GND

Id: 3/5 Title: MicroMod Function Board

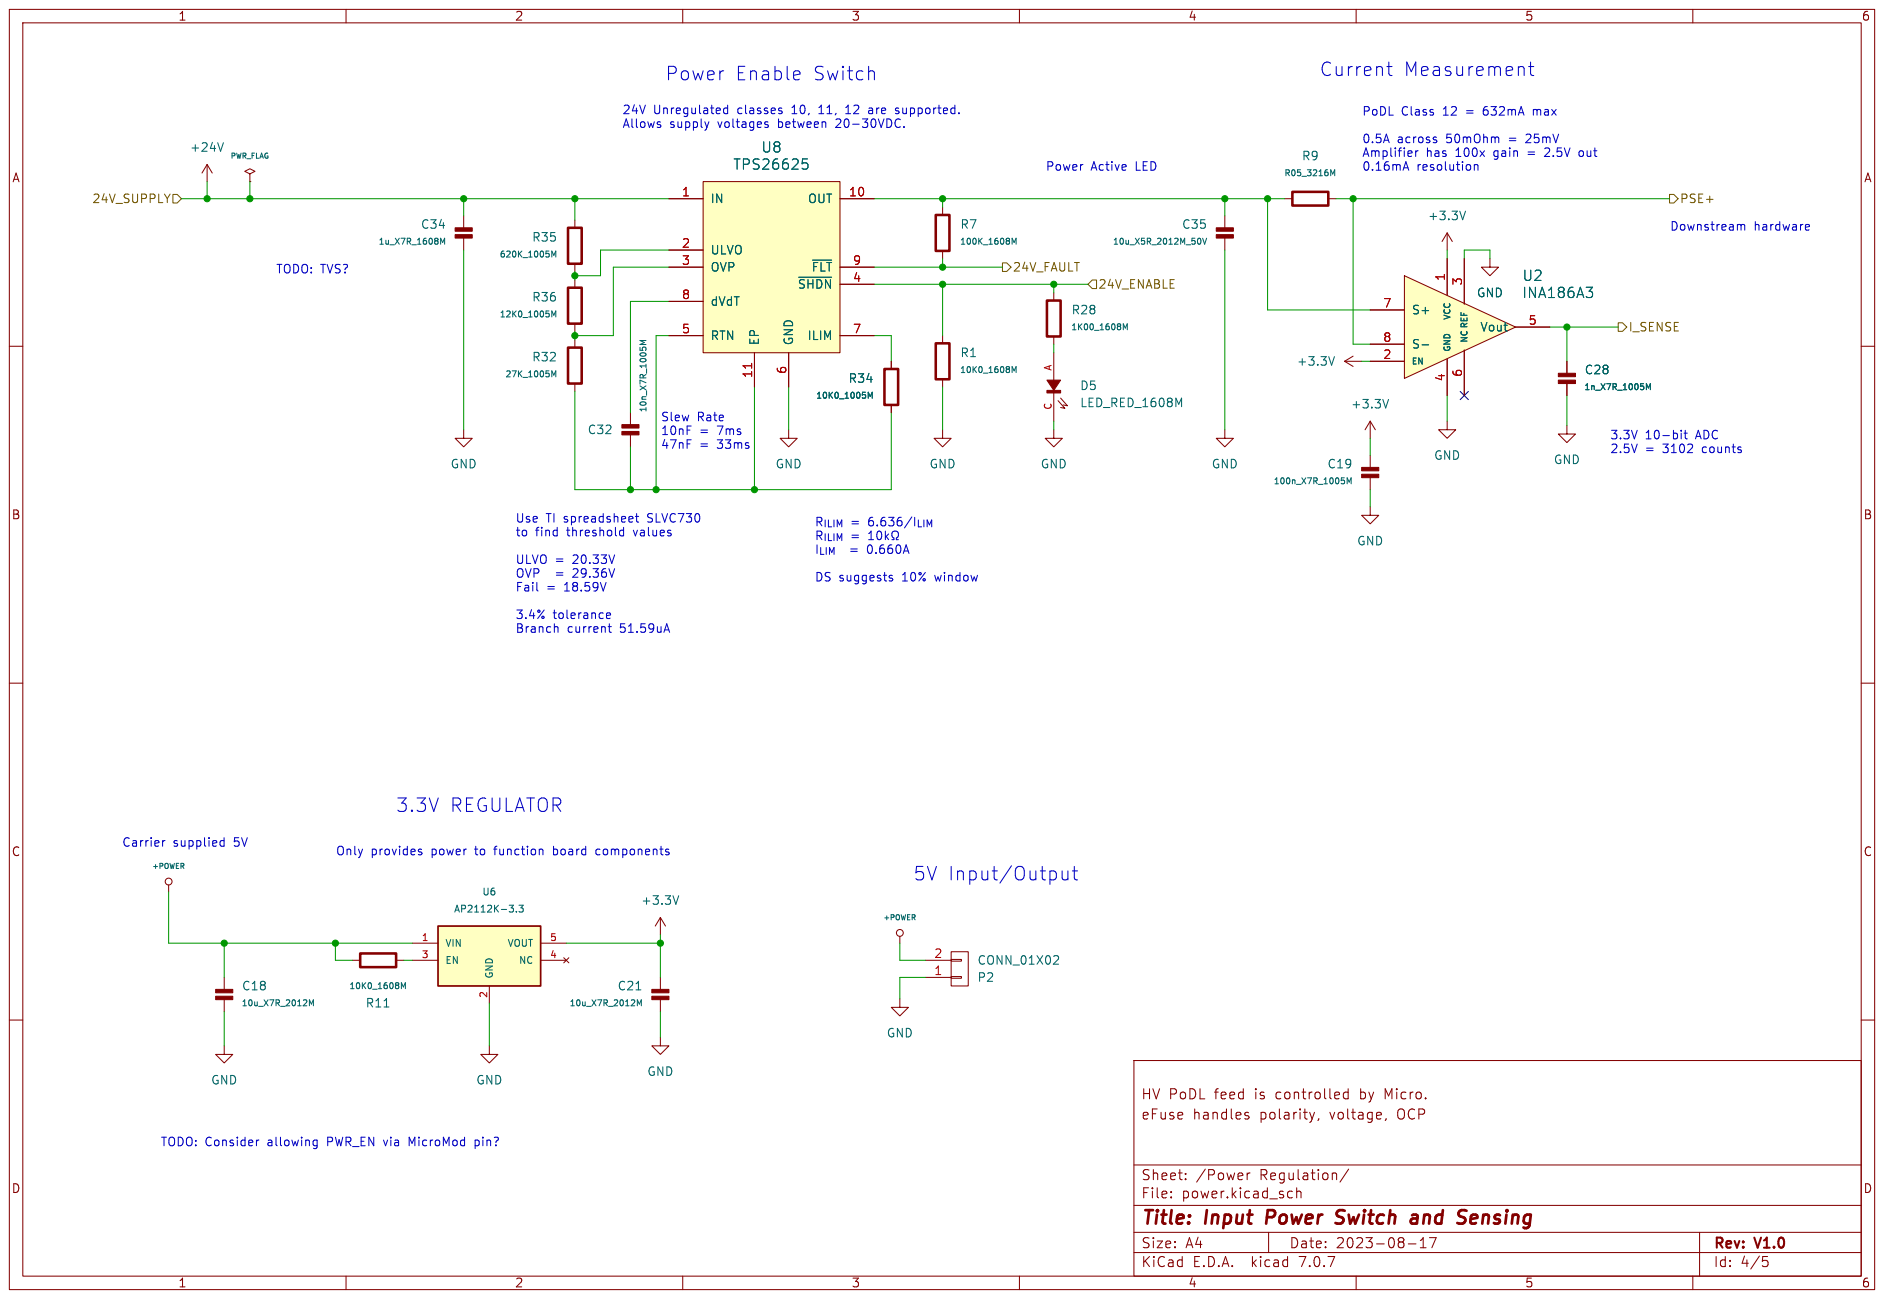
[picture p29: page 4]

Power Active LED Power Enable Switch

2 EN 3 NC 4 VOUT 5 U6 AP2112K-3.3 GND

Id: 4/5 Title: Input Power Switch and Sensing

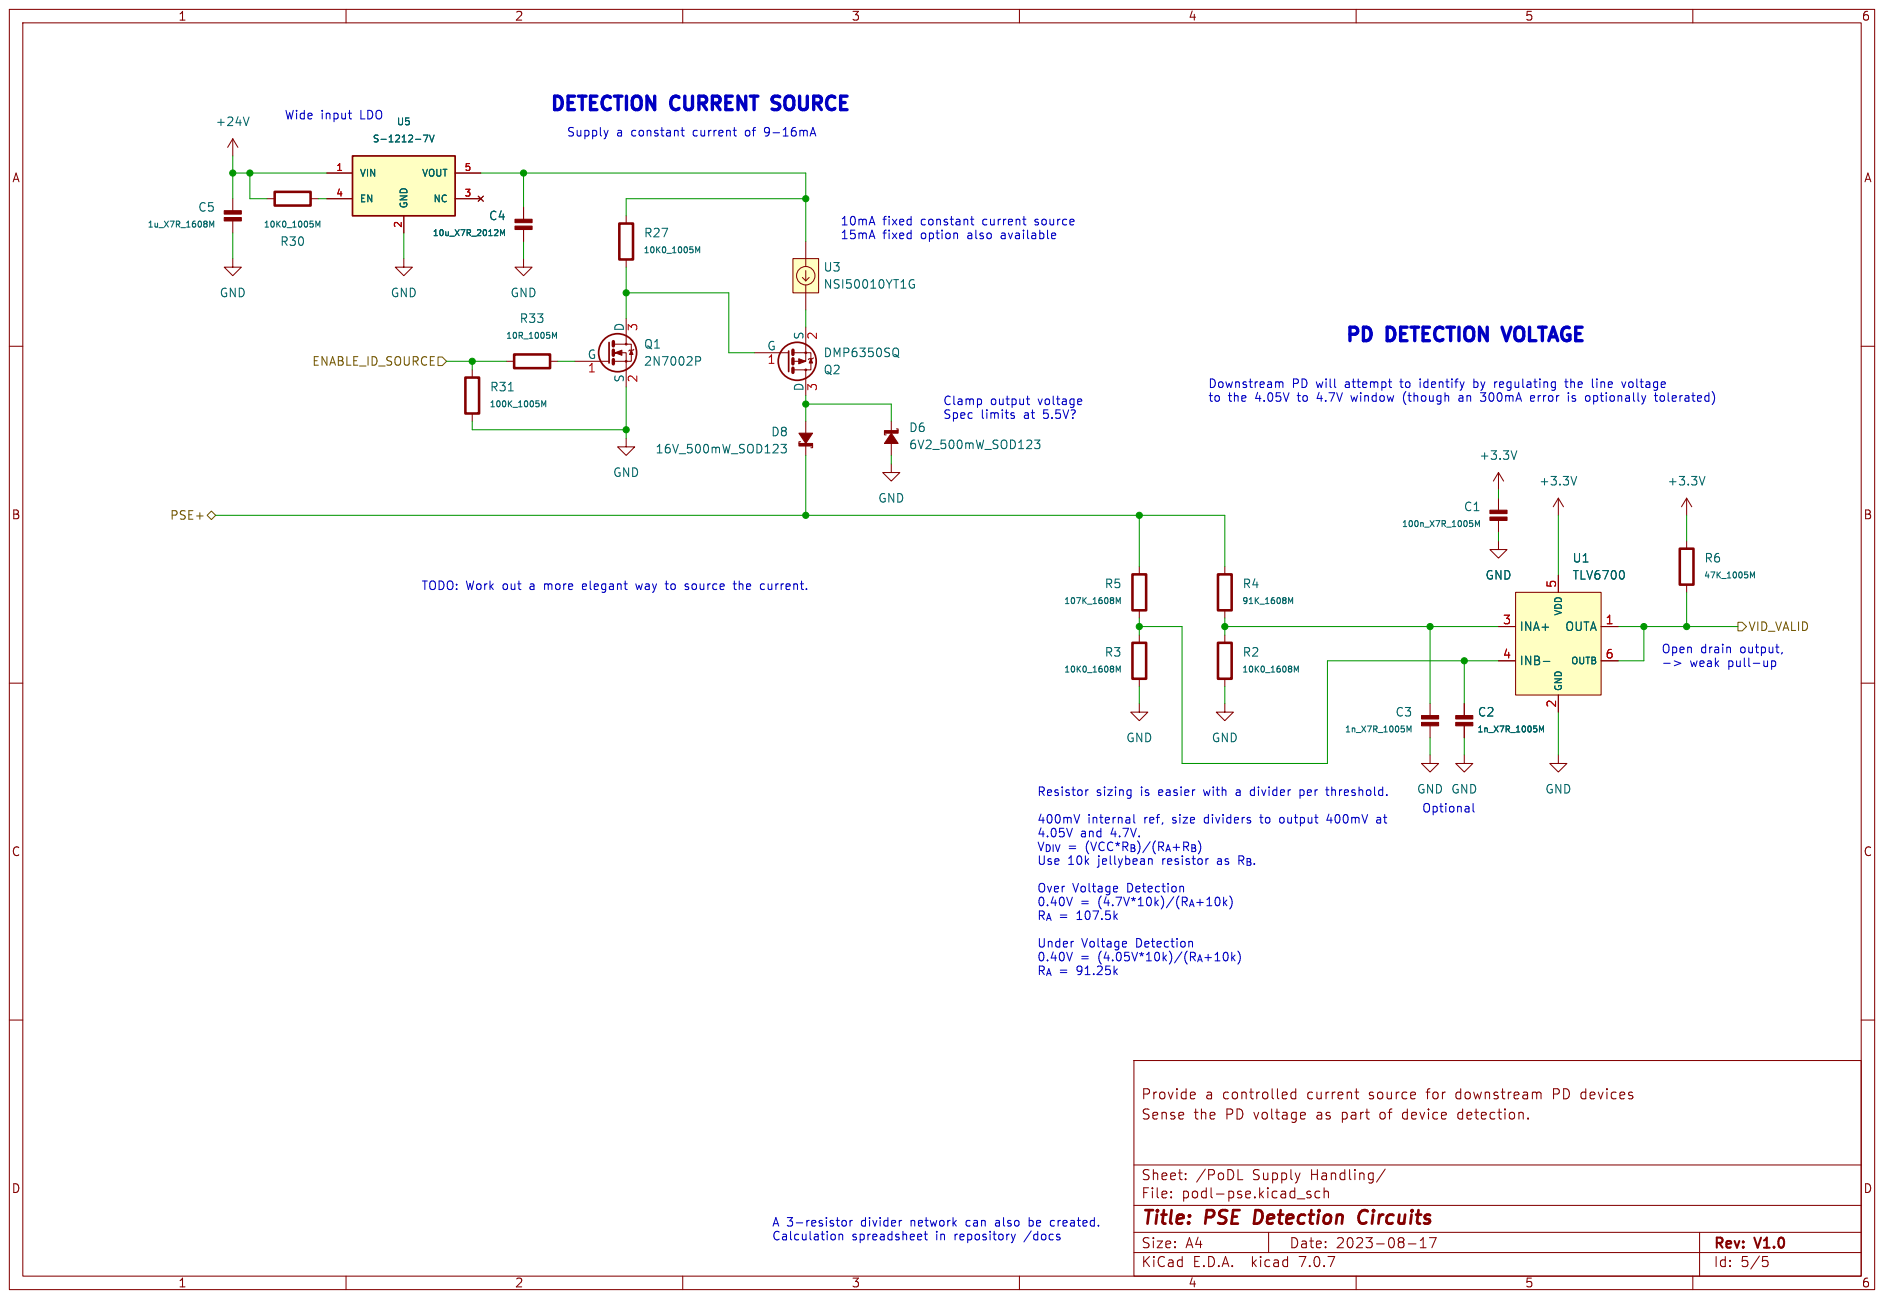
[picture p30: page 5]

2 NC 3 EN 4 VOUT 5 U5 S-1212-7V GND

15mA fixed option also available Clamp output voltage

Id: 5/5 Title: PSE Detection Circuits

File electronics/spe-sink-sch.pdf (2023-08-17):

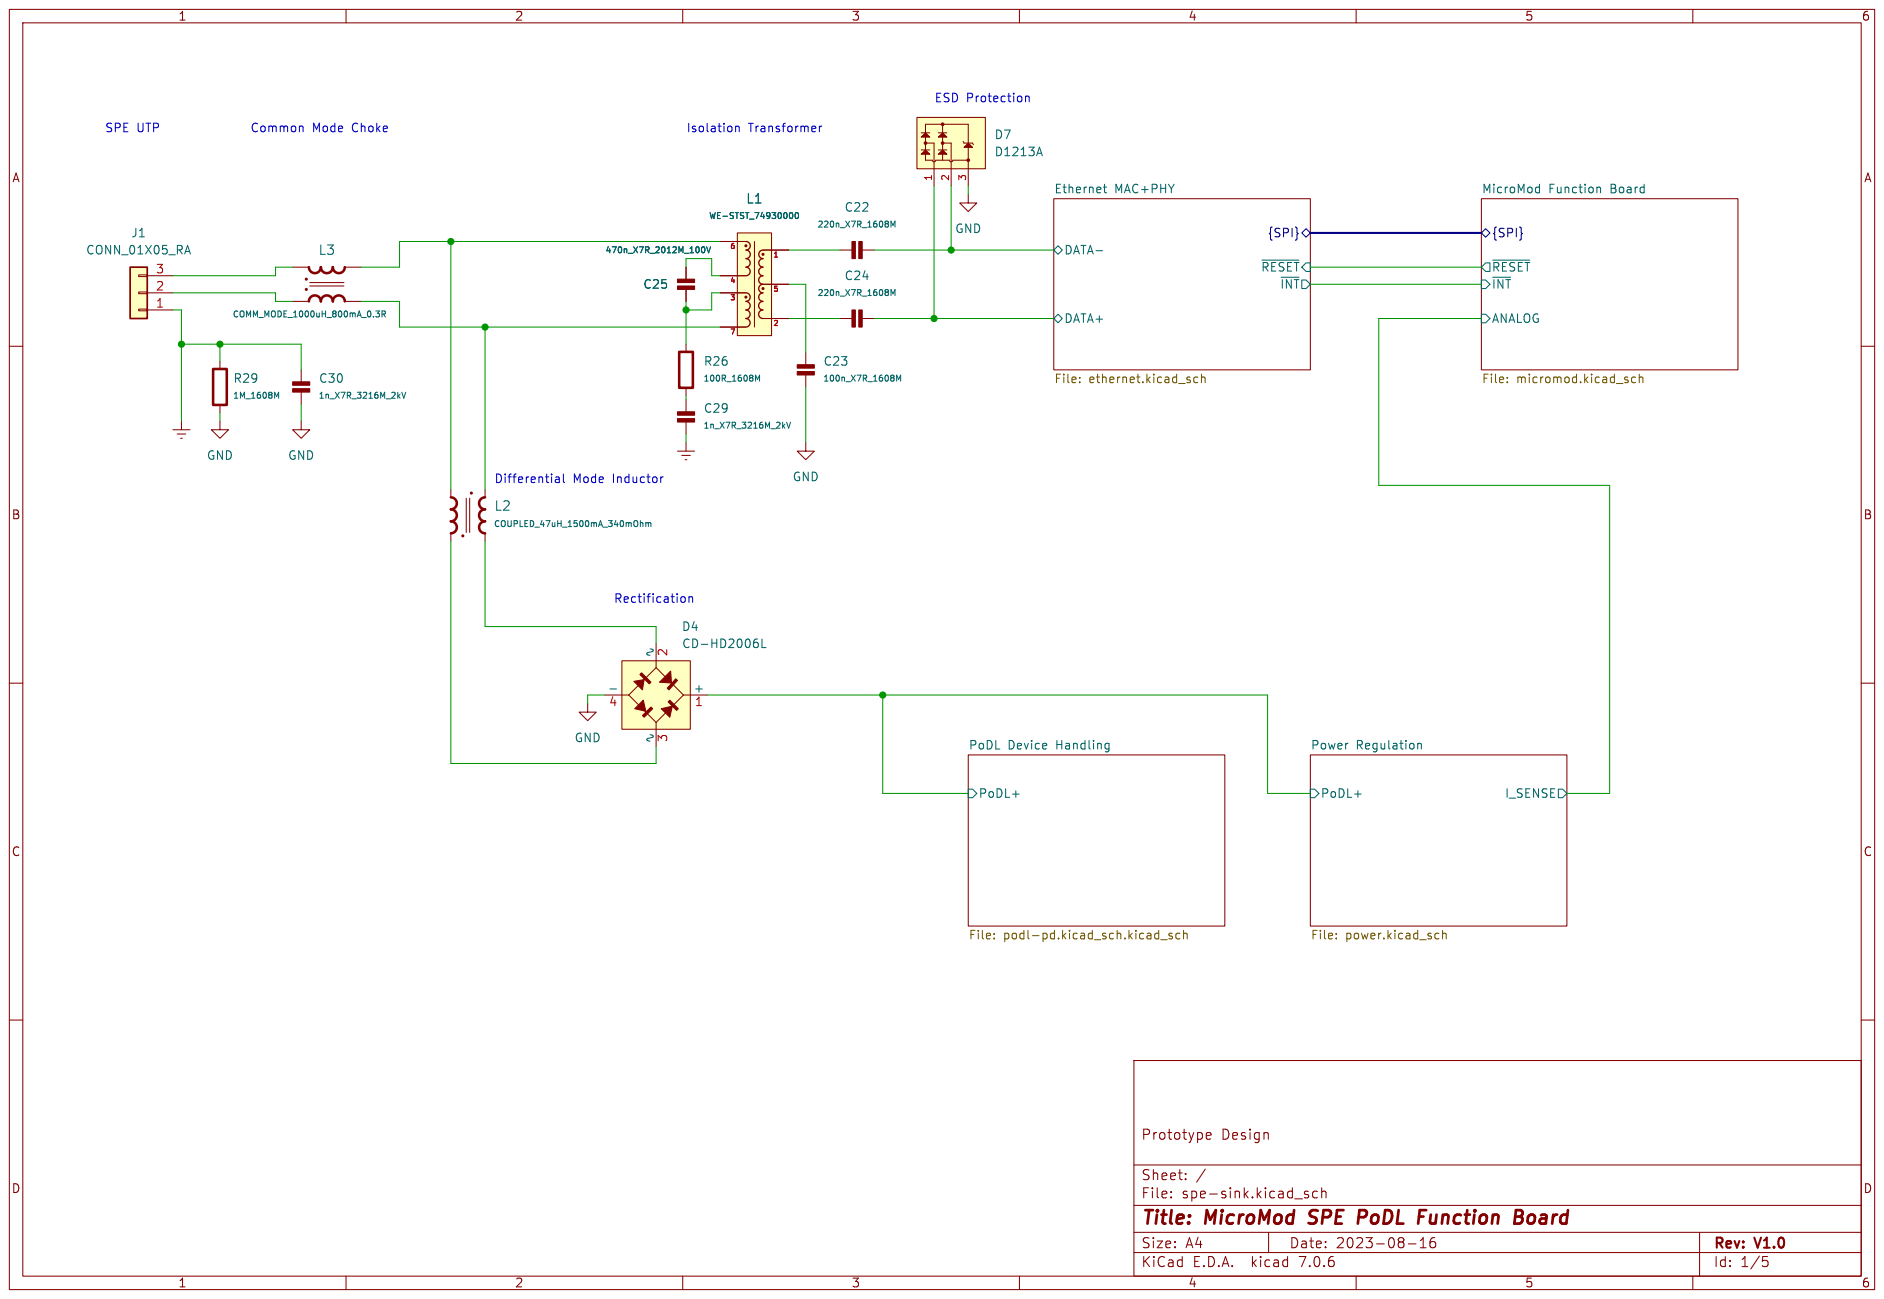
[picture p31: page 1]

~{INT} DATA+ DATA- Ethernet MAC+PHY

Power Regulation File: power.kicad_sch L2

Id: 1/5 Title: MicroMod SPE PoDL Function Board

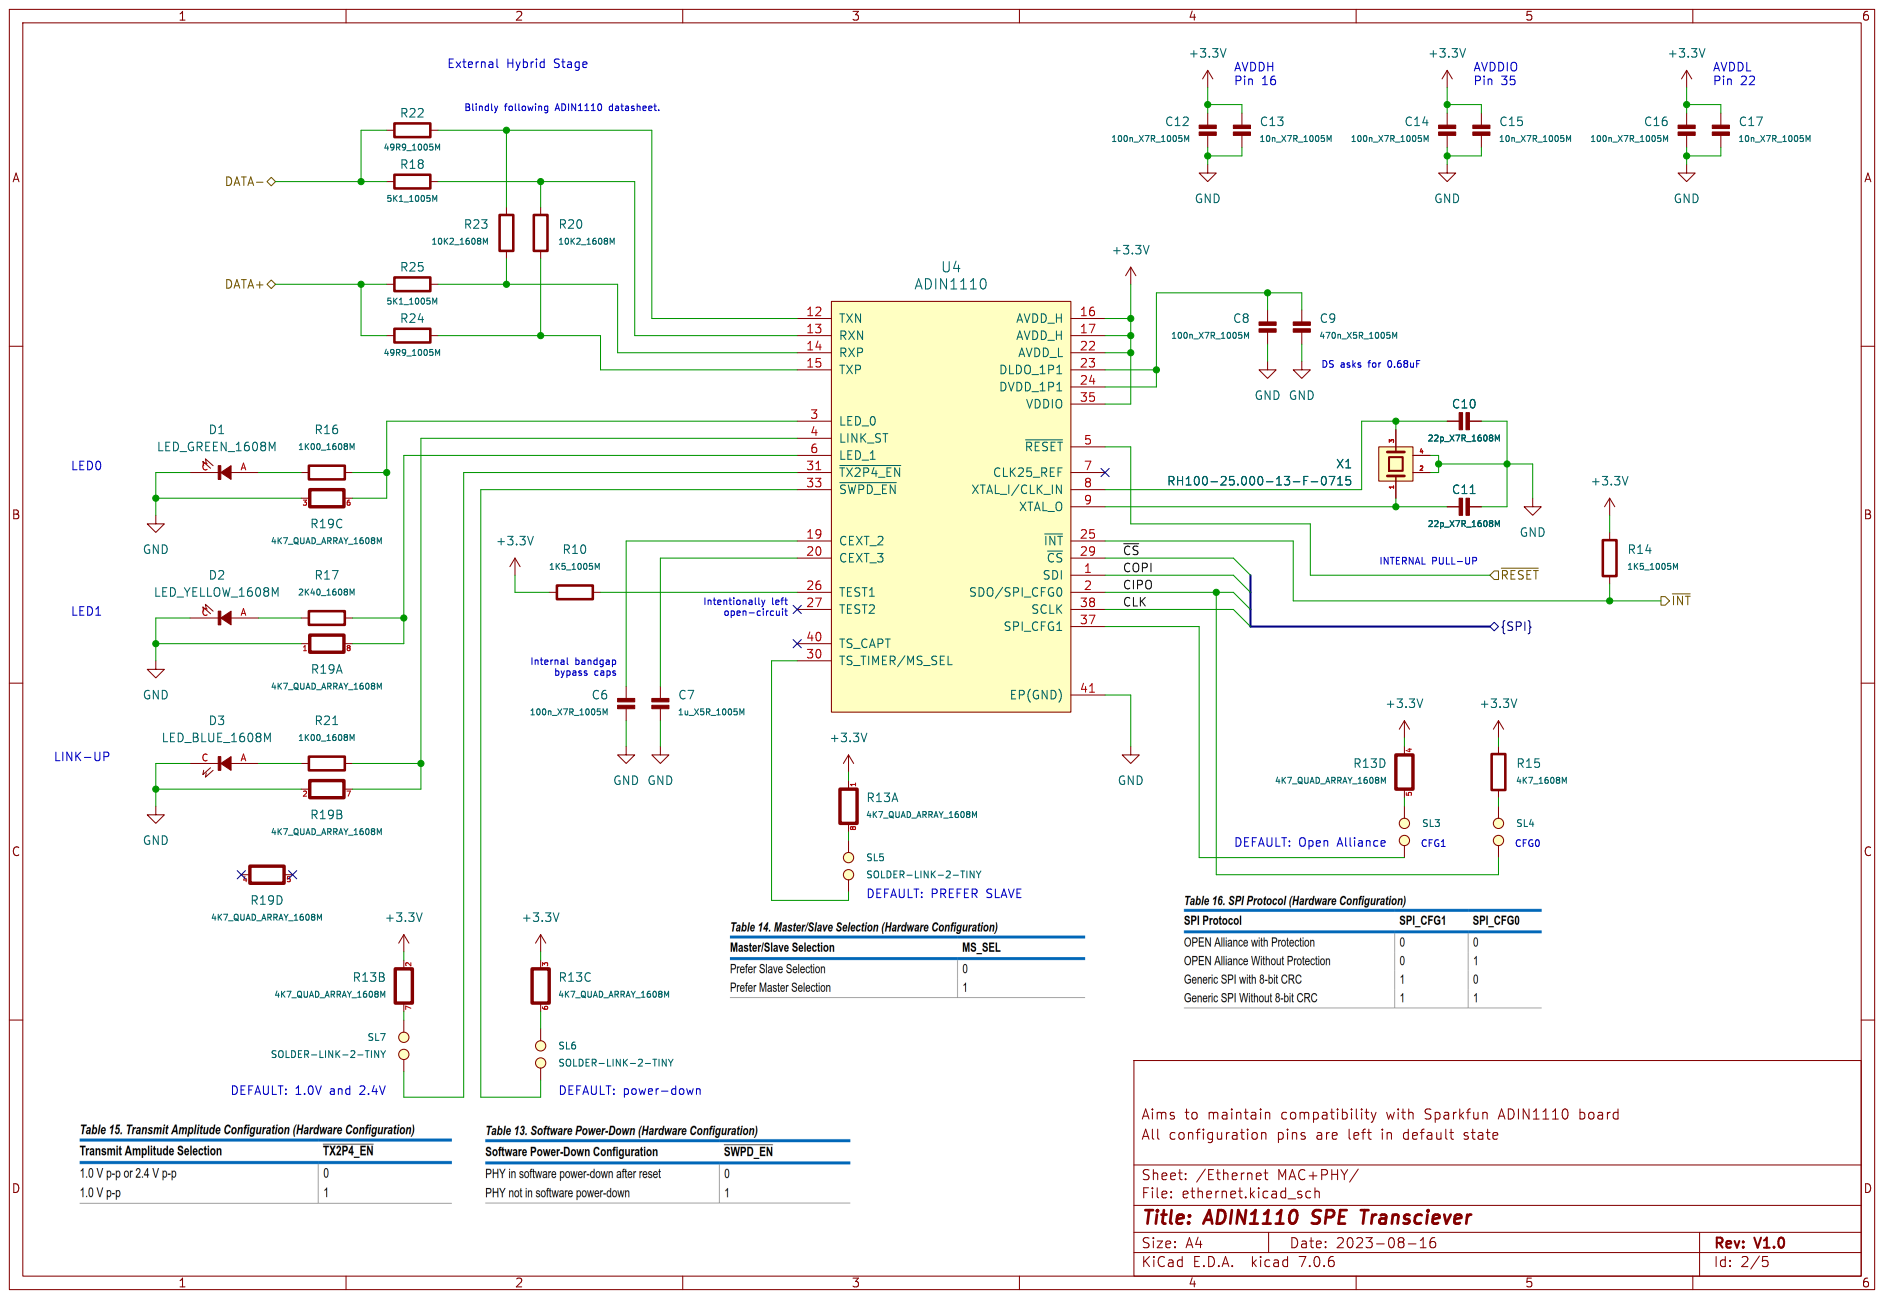
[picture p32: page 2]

Pin 35 DS asks for 0.68uF DEFAULT: Open Alliance DEFAULT: PREFER SLAVE

SL5 SOLDER-LINK-2-TINY GND

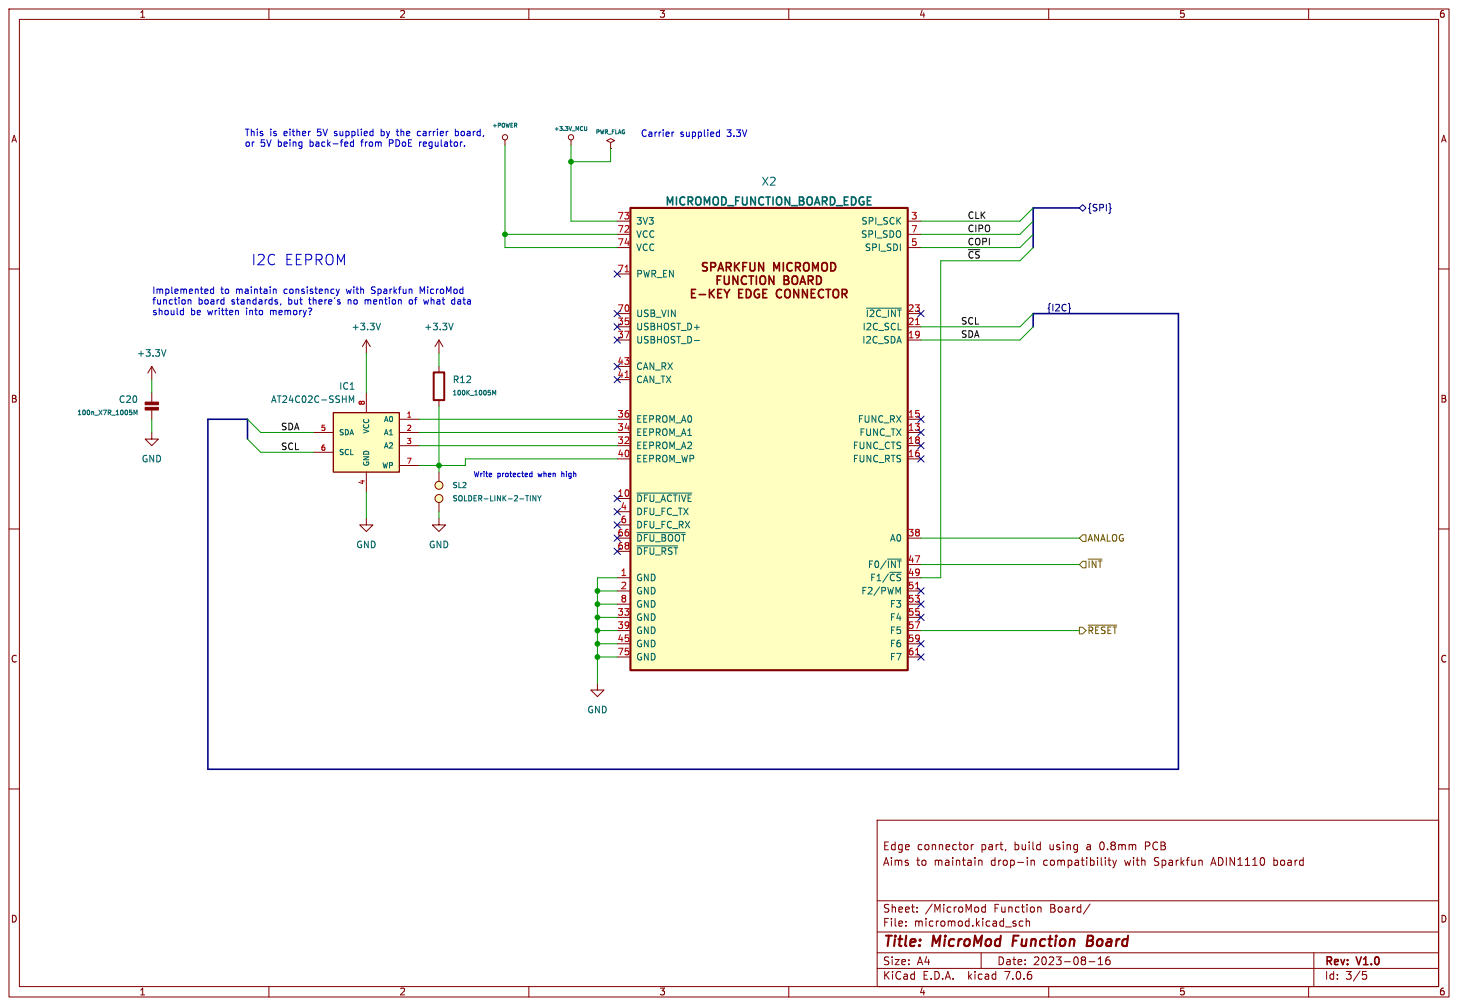
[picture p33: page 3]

+POWER SL2 SOLDER-LINK-2-TINY

should be written into memory?

4 SDA 5 SCL 6 WP 7 VCC

Id: 3/5 Title: MicroMod Function Board

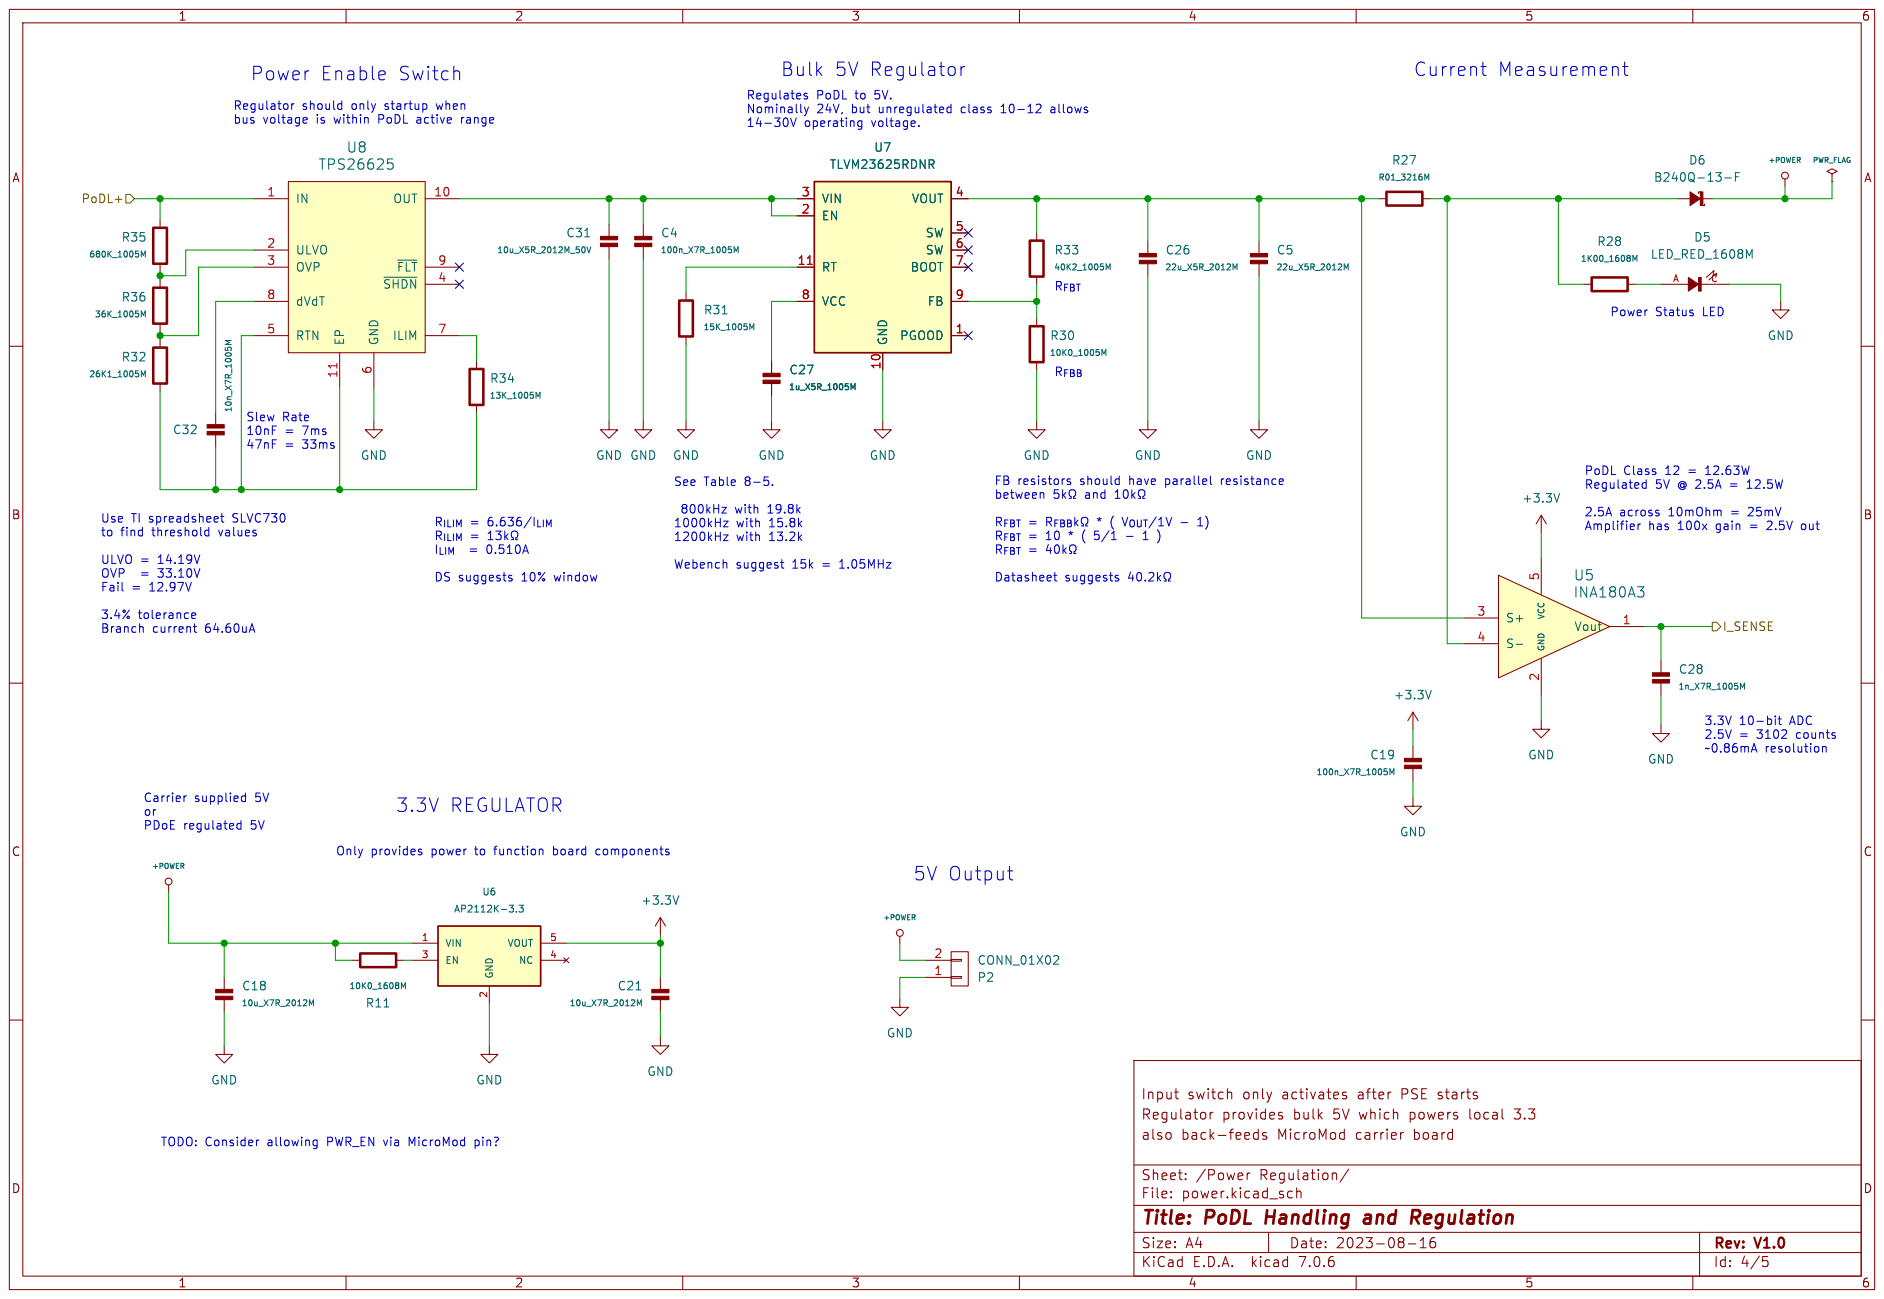
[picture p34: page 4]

2.5V = 3102 counts ~0.86mA resolution Power Enable Switch

between þÿ5k©and þÿ10k©

R_{ILIM} = 6.636/I_{LIM}
R_{ILIM} = þÿ13k©
I_{LIM}= 0.510A DS suggests 10% window

Id: 4/5 Title: PoDL Handling and Regulation

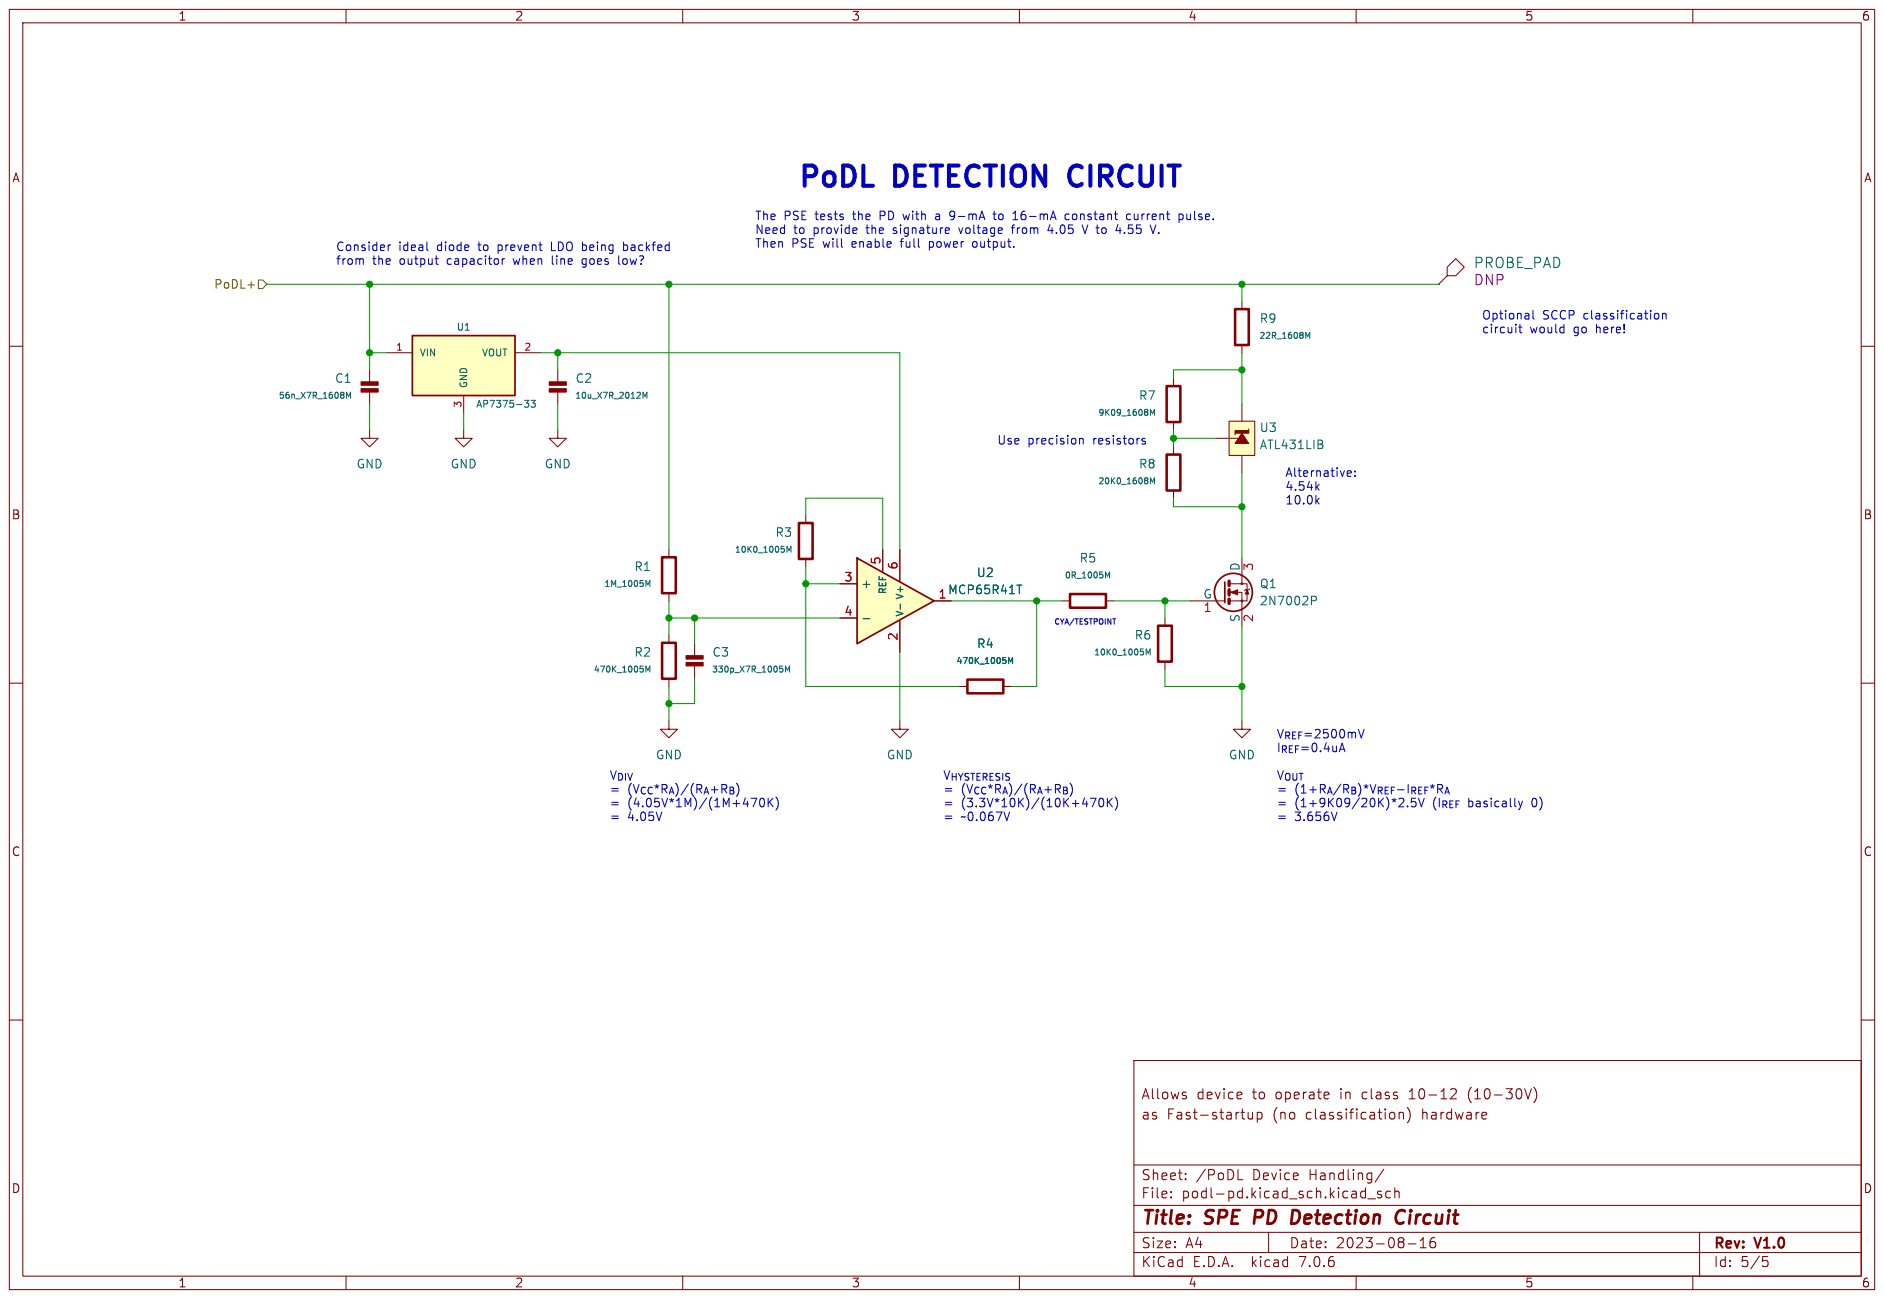
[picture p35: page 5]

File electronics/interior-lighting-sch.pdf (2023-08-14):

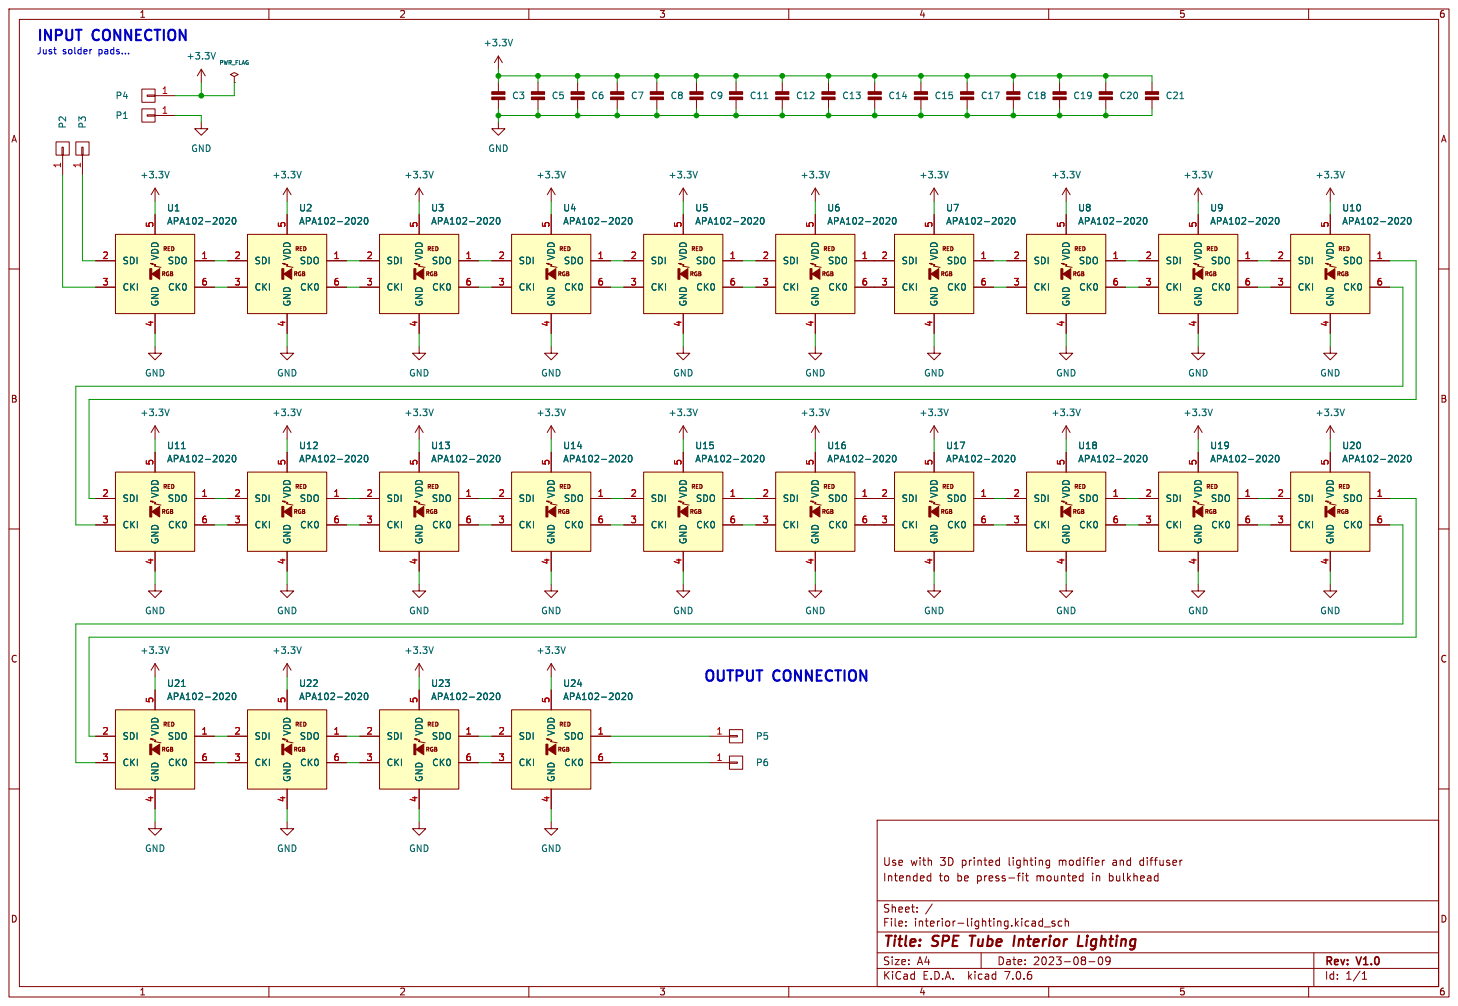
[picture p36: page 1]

5 CK0 6 U1APA102-2020 SDO 1 SDI 2 CKI 3 GND

5 CK0 6 U6APA102-2020 SDO 1 SDI 2 CKI 3 GND

5 CK0 6 U3APA102-2020 SDO 1 SDI 2 CKI 3 GND

5 CK0 6 U4APA102-2020 SDO 1 SDI 2 CKI 3 GND

5 CK0 6 U7APA102-2020 SDO 1 SDI 2 CKI 3 GND

5 CK0 6 U8APA102-2020 SDO 1 SDI 2 CKI 3 GND

5 CK0 6 U10 APA102-2020 SDO 1 SDI 2 CKI 3 GND

5 CK0 6 U9APA102-2020 SDO 1 SDI 2 CKI 3 GND

5 CK0 6 U12 APA102-2020 SDO 1 SDI 2 CKI 3 GND

5 CK0 6 U13 APA102-2020 SDO 1 SDI 2 CKI 3 GND

5 CK0 6 U15 APA102-2020 SDO 1 SDI 2 CKI 3 GND

5 CK0 6 U17 APA102-2020 SDO 1 SDI 2 CKI 3 GND

5 CK0 6 U18 APA102-2020 SDO 1 SDI 2 CKI 3 GND

5 CK0 6 U11 APA102-2020 SDO 1 SDI 2 CKI 3 GND

5 CK0 6 U14 APA102-2020 SDO 1 SDI 2 CKI 3 GND

5 CK0 6 U16 APA102-2020 SDO 1 SDI 2 CKI 3 GND

5 CK0 6 U19 APA102-2020 SDO 1 SDI 2 CKI 3 GND

5 CK0 6 U20 APA102-2020 SDO 1 SDI 2 CKI 3 GND

5 CK0 6 U24 APA102-2020 SDO 1 SDI 2 CKI 3 GND

5 CK0 6 U21 APA102-2020 SDO 1 SDI 2 CKI 3 GND

5 CK0 6 U22 APA102-2020 SDO 1 SDI 2 CKI 3 GND

5 CK0 6 U23 APA102-2020 SDO 1 SDI 2 CKI 3 GND

File: interior-lighting.kicad_sch Sheet: /
Id: 1/1 Title: SPE Tube Interior Lighting

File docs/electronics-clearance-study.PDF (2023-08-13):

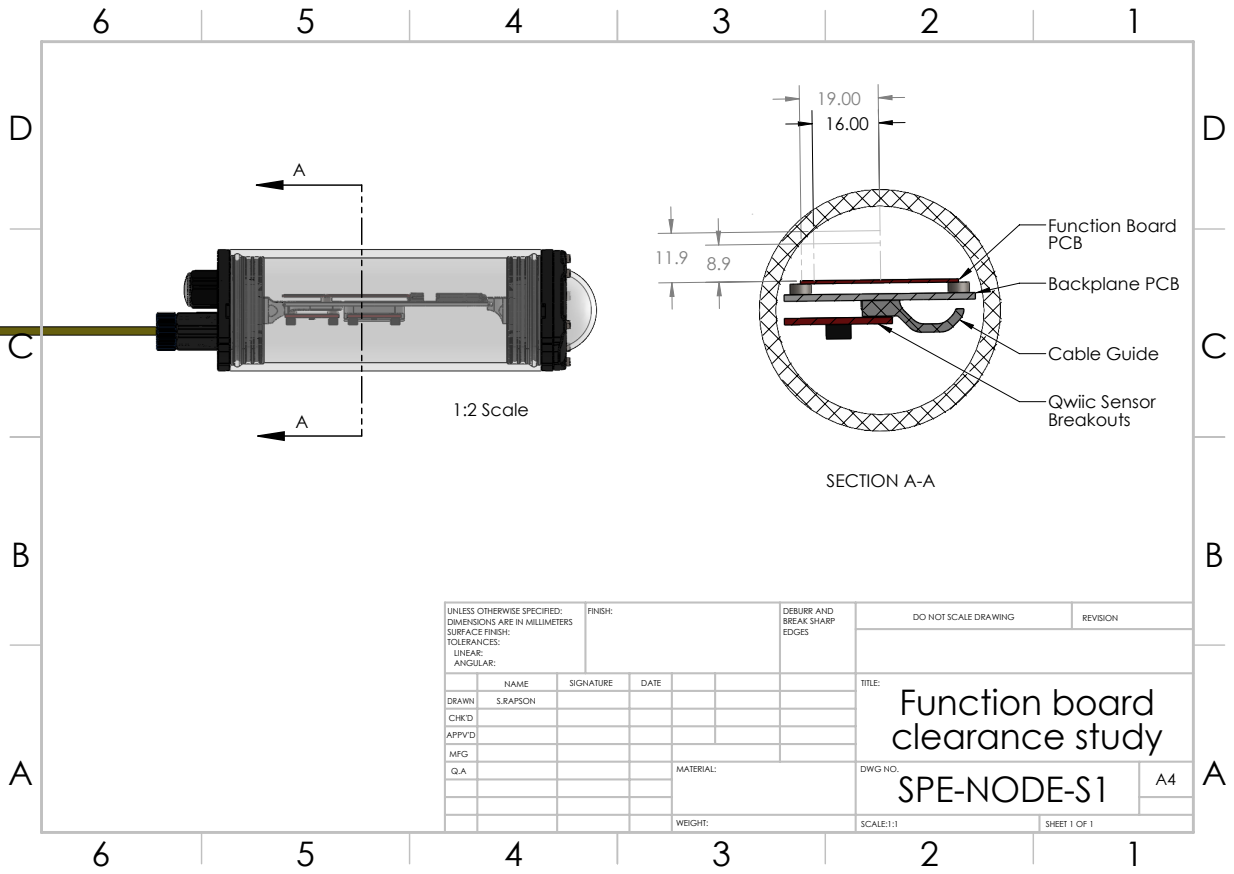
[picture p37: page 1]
1:2 Scale; SECTION A-A; Function Board; Cable Guide; Qwiic Sensor; Backplane PCB; FINISH:; DEBURR AND; BREAK SHARP; DO NOT SCALE DRAWING; REVISION; SCALE:1:1; SHEET 1 OF 1

UNLESS OTHERWISE SPECIFIED:
DIMENSIONS ARE IN MILLIMETERS
SURFACE FINISH:
TOLERANCES:
LINEAR:
ANGULAR:

NAME | SIGNATURE | DATE | | | | TITLE: Function board clearance study

DRAWN | S.RAPSON
CHK'D
APPV'D
MFG
Q.A | | | | MATERIAL: | DWG NO. SPE-NODE-S1 | A4

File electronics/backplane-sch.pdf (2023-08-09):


SPI1{SPI} PWM1 D1 ADC1 Processor File: processor.kicad_sch

Power Regulation File: power.kicad_sch

{USB} USB Input File: usb-input.kicad_sch

File: backplane.kicad_sch Sheet: /
Id: 1/6 Title: SPE-NODE-BACKPLANE


Id: 2/6 Title: USB CONNECTION


3V3_EN is left NC because most MicroMod

i.e. 1.66V for 5V input I2C BUS MERGE RESET/BOOT BUTTONS

~{BOOT}
+POWER SL4 SOLDER-LINK-2-TINY

If joining the bus wiring, first cut I2C1 from


SCL CAN.RX CAN.TX
SPARKFUN MICROMOD

that doesn't use them

Id: 4/6 Title: MicroMod Function Board


Id: 5/6 Title: Expansion IO


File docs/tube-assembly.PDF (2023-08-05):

OPTIONAL CAMERA OR SPECTROMETER; DO NOT SCALE DRAWING; REVISION; PROPOSED WATERPROOF CAPSULE CONFIGURATION

TETHER/NETWORK CABLE
PRESSURE/TEMP SENSOR
EXT. STATUS LED
RELIEF VALVE

DWG NO. | A4 SPE-NODE-P1

SCALE:1:1 | SHEET 1 OF 1

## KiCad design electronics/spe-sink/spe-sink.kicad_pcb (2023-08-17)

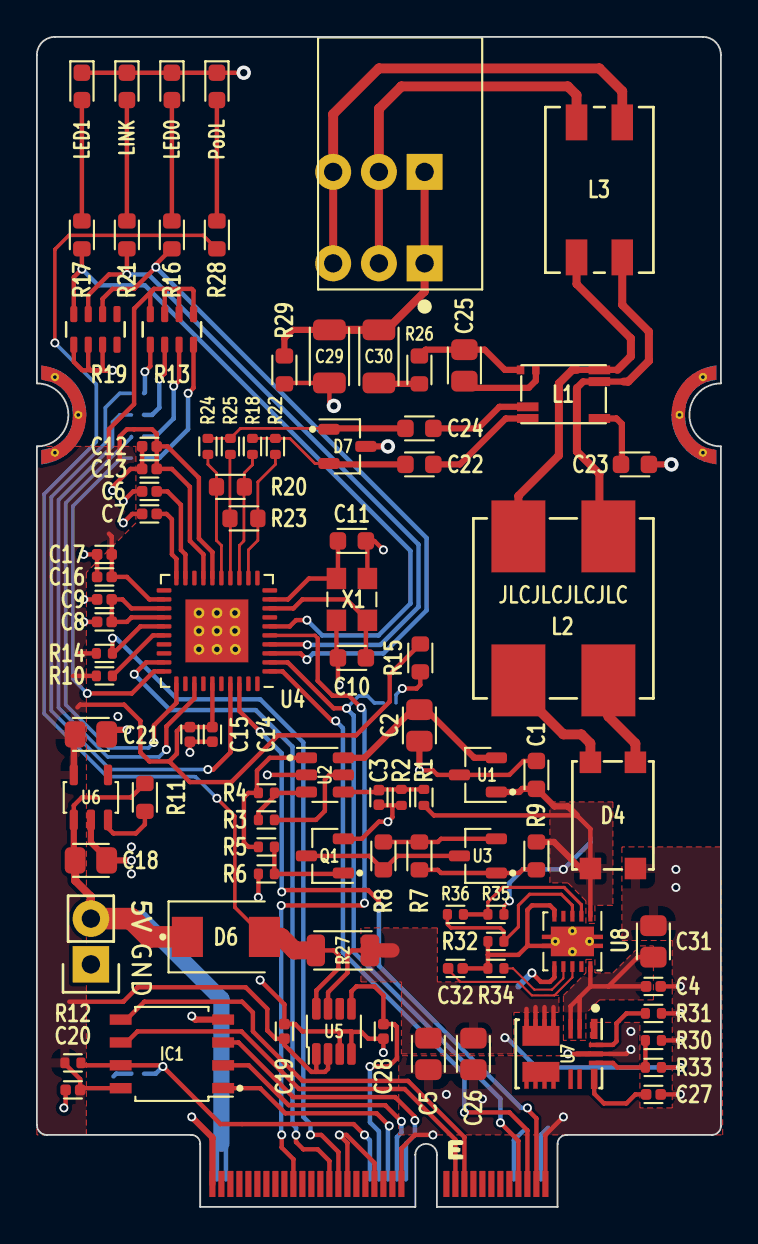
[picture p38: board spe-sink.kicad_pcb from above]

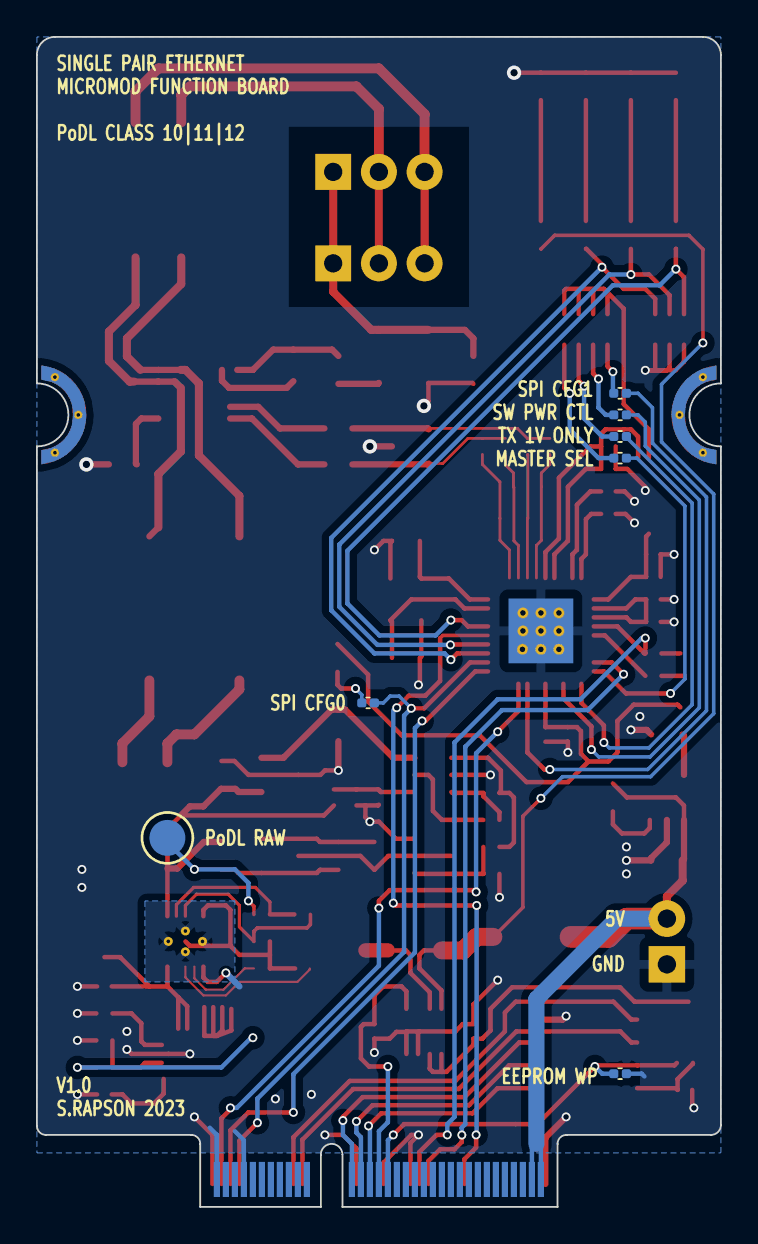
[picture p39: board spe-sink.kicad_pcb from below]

Board: 2 copper layers, 38.0 x 65.0 mm, 99 parts (7 on the bottom side), 79 nets.

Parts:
C1: 56n_X7R_1608M; CAPC1608X90N
C2, C18, C21: 10u_X7R_2012M; CAPC2012X110N
C3: 330p_X7R_1005M; CAPC1005X60N
C4, C6, C8, C12, C14, C16, C19, C20: 100n_X7R_1005M; CAPC1005X60N
C5, C26: 22u_X5R_2012M; CAPC2012X110N
C7, C27: 1u_X5R_1005M; CAPC1005X60N
C9: 470n_X5R_1005M; CAPC1005X60N
C10, C11: 22p_X7R_1608M; CAPC1608X90N
C13, C15, C17, C32: 10n_X7R_1005M; CAPC1005X60N
C22, C24: 220n_X7R_1608M; CAPC1608X90N
C23: 100n_X7R_1608M; CAPC1608X90N
C25: 470n_X7R_2012M_100V; CAPC2012X110N
C28: 1n_X7R_1005M; CAPC1005X60N
C29, C30: 1n_X7R_3216M_2kV; CAPC3216X135N
C31: 10u_X5R_2012M_50V; CAPC2012X110N
D1: LED_GREEN_1608M; LEDC1608X80L40N
D2: LED_YELLOW_1608M; LEDC1608X80L40N
D3: LED_BLUE_1608M; LEDC1608X80L40N
D4: CD-HD2006L; CD-HD2x(L)
D5: LED_RED_1608M; LEDC1608X80L40N
D6: B240Q-13-F; SODFL5436X262N
D7: D1213A; SOT95P240X110-3L16N
IC1: AT24C02C-SSHM; SOIC127P600X330-8L2N
J1: CONN_01X05_RA; CUI_TBL009-254-03
L1: WE-STST_74930000; WE-STST
L2: COUPLED_47uH_1500mA_340mOhm; WE-MCRI-1040
L3: COMM_MODE_1000uH_800mA_0.3R; WE-SL2
P2: CONN_01X02; 61300211121
Q1: 2N7002P; SOT95P240X110-3L16N
R1: 1M_1005M; RESC1005X40N
R2, R4: 470K_1005M; RESC1005X40N
R3, R6, R30: 10K0_1005M; RESC1005X40N
R5: 0R_1005M; RESC1005X40N
R7: 9K09_1608M; RESC1608X50N
R8: 20K0_1608M; RESC1608X50N
R9: 22R_1608M; RESC1608X50N
R10, R14: 1K5_1005M; RESC1005X40N
R11: 10K0_1608M; RESC1608X50N
R12: 100K_1005M; RESC1005X40N
R13, R19: 4K7_QUAD_ARRAY_1608M; R_Array_Concave_4x1608M
R15: 4K7_1608M; RESC1608X50N
R16, R21, R28: 1K00_1608M; RESC1608X50N
R17: 2K40_1608M; RESC1608X50N
R18, R25: 5K1_1005M; RESC1005X40N
R20, R23: 10K2_1608M; RESC1608X50N
R22, R24: 49R9_1005M; RESC1005X40N
R26: 100R_1608M; RESC1608X50N
R27: R01_3216M; RESC3216X60N
R29: 1M_1608M; RESC1608X50N
R31: 15K_1005M; RESC1005X40N
R32: 26K1_1005M; RESC1005X40N
R33: 40K2_1005M; RESC1005X40N
R34: 13K_1005M; RESC1005X40N
R35: 680K_1005M; RESC1005X40N
R36: 36K_1005M; RESC1005X40N
SL2, SL3, SL4, SL5, SL6, SL7: SOLDER-LINK-2-TINY; SJ1005-2N
TEST1: PROBE_PAD; TP200
U1: AP7375-33; SOT95P240X110-3L16N
U2: MCP65R41T; SOT95P240X110-6L16N
U3: ATL431LIB; SOT95P240X110-3L16N
U4: ADIN1110; QFN50P600X600X100-40T350X350N
U5: INA186A3; SOT23-8P65_280X145L45X30N
U6: AP2112K-3.3; SOT95P280X145-5L30N
U7: TLVM23625RDNR; QFN50P450X350X200-11-FCMOD11
U8: TPS26625; SON50P300X300X90-11T240X165N_RELIEF
X1: RH100-25.000-13-F-0715; OSCCC320X250X60L90X100N
X2: MICROMOD_FUNCTION_BOARD_EDGE; M.2-MICROMOD-FN-CARD-EDGE

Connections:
+3.3V: C12.1, C13.1, C14.1, C15.1, C16.1, C17.1, C19.1, C20.1, C21.1, IC1.8 (VCC), R10.1, R12.1, R13.1, R13.2, R13.3, R13.4, R14.1, R15.1, U4.16 (AVDD_H), U4.17 (AVDD_H), U4.22 (AVDD_L), U4.35 (VDDIO), U5.1 (VCC), U5.2 (EN), U6.5 (VOUT)
+POWER: C18.1, D6.C, P2.2, R11.1, U6.1 (VIN), X2.72 (VCC), X2.74 (VCC)
/Ethernet MAC+PHY/CIPO: SL4.1, U4.2 (SDO/SPI_CFG0), X2.7 (SPI_SDO)
/Ethernet MAC+PHY/CLK: U4.38 (SCLK), X2.3 (SPI_SCK)
/Ethernet MAC+PHY/COPI: U4.1 (SDI), X2.5 (SPI_SDI)
/Ethernet MAC+PHY/DATA+: C24.2, D7.1 (A1), R24.1, R25.1
/Ethernet MAC+PHY/DATA-: C22.2, D7.2 (C2), R18.1, R22.1
/Ethernet MAC+PHY/~CS: U4.29 (~CS), X2.49 (F1/~CS)
/Ethernet MAC+PHY/~INT: R14.2, U4.25 (~INT), X2.47 (F0/~INT)
/Ethernet MAC+PHY/~RESET: U4.5 (~RESET), X2.57 (F5)
/MicroMod Function Board/ANALOG: C28.1, U5.5 (Vout), X2.38 (A0)
/MicroMod Function Board/SCL: IC1.6 (SCL), X2.21 (I2C_SCL)
/MicroMod Function Board/SDA: IC1.5 (SDA), X2.19 (I2C_SDA)
/PoDL Device Handling/PoDL+: C1.1, D4.1 (+), R1.1, R9.1, R35.1, TEST1.1 (PAD), U1.1 (VIN), U8.1 (IN)
Earth: C29.2, C30.1, J1.1, R29.1
GND: C1.2, C2.2, C3.2, C4.2, C5.2, C6.2, C7.2, C8.2, C9.2, C10.2, C11.2, C12.2, C13.2, C14.2, C15.2, C16.2, C17.2, C18.2, C19.2, C20.2, C21.2, C23.2, C26.2, C27.2, C28.2, C30.2, C31.2, D1.C, D2.C, D3.C, D4.4 (-), D5.C, D7.3, IC1.4 (GND), P2.1, Q1.2 (S), R2.2, R6.2, R19.1, R19.2, R19.3, R29.2, R30.2, R31.2, SL2.2, U1.3 (GND), U2.2 (V-), U4.41 (EP(GND)), U5.3 (REF), U5.4 (GND), U6.2 (GND), U7.10 (GND), U8.6 (GND), X1.2, X1.4, X2.1 (GND), X2.2 (GND), X2.8 (GND), X2.33 (GND), X2.39 (GND), X2.45 (GND), X2.75 (GND)
unnamed: C22.1, L1.1
unnamed: C23.1, L1.5
unnamed: C24.1, L1.2
unnamed: C25.1, L1.4
unnamed: C25.2, L1.3, R26.1
unnamed: C29.1, R26.2
unnamed: D1.A, R16.1
unnamed: D2.A, R17.1
unnamed: D3.A, R21.1
unnamed: D4.2 (∿), L2.4
unnamed: D4.3 (∿), L2.1
unnamed: D5.A, R28.2
unnamed: IC1.1 (A0), X2.36 (EEPROM_A0)
unnamed: IC1.2 (A1), X2.34 (EEPROM_A1)
unnamed: IC1.3 (A2), X2.32 (EEPROM_A2)
unnamed: IC1.7 (WP), R12.2, SL2.1, X2.40 (EEPROM_WP)
unnamed: J1.2, L3.2
unnamed: J1.3, L3.1
unnamed: L1.6, L2.2, L3.4
unnamed: L1.7, L2.3, L3.3
unnamed: Q1.3 (D), R8.2, U3.3 (A)
unnamed: Q1.1 (G), R5.2, R6.1
unnamed: R4.2, R5.1, U2.1
unnamed: R13.5, SL3.2
unnamed: R13.6, SL6.2
unnamed: R13.7, SL7.2
unnamed: R13.8, SL5.2
unnamed: R15.2, SL4.2
unnamed: C2.1, U1.2 (VOUT), U2.6 (V+)
unnamed: R3.2, R4.1, U2.3 (+)
unnamed: C3.1, R1.2, R2.1, U2.4 (-)
unnamed: R3.1, U2.5 (REF)
unnamed: R7.1, R9.2, U3.1 (C)
unnamed: R7.2, R8.1, U3.2 (REF)
unnamed: C6.1, U4.19 (CEXT_2)
unnamed: C7.1, U4.20 (CEXT_3)
unnamed: C8.1, C9.1, U4.23 (DLDO_1P1), U4.24 (DVDD_1P1)
unnamed: R16.2, R19.6, U4.3 (LED_0)
unnamed: R17.2, R19.8, U4.6 (LED_1)
unnamed: R19.7, R21.2, U4.4 (LINK_ST)
unnamed: R18.2, R20.1, U4.13 (RXN)
unnamed: R23.2, R25.2, U4.14 (RXP)
unnamed: SL3.1, U4.37 (SPI_CFG1)
unnamed: R10.2, U4.26 (TEST1)
unnamed: SL5.1, U4.30 (TS_TIMER/MS_SEL)
unnamed: R22.2, R23.1, U4.12 (TXN)
unnamed: R20.2, R24.2, U4.15 (TXP)
unnamed: C10.1, U4.8 (XTAL_I/CLK_IN), X1.3
unnamed: C11.1, U4.9 (XTAL_O), X1.1
unnamed: SL6.1, U4.33 (~SWPD_EN)
unnamed: SL7.1, U4.31 (~TX2P4_EN)
unnamed: C5.1, C26.1, R27.1, R33.1, U5.7 (S+), U7.4 (VOUT)
unnamed: D6.A, R27.2, R28.1, U5.8 (S-)
unnamed: R11.2, U6.3 (EN)
unnamed: C4.1, C31.1, U7.2 (EN), U7.3 (VIN), U8.10 (OUT)
unnamed: R30.1, R33.2, U7.9 (FB)
unnamed: R31.1, U7.11 (RT)
unnamed: C27.1, U7.8 (VCC)
unnamed: C32.2, R32.2, R34.2, U8.5 (RTN), U8.11 (EP)
unnamed: R34.1, U8.7 (ILIM)
unnamed: R32.1, R36.2, U8.3 (OVP)
unnamed: R35.2, R36.1, U8.2 (ULVO)
unnamed: C32.1, U8.8 (dVdT)

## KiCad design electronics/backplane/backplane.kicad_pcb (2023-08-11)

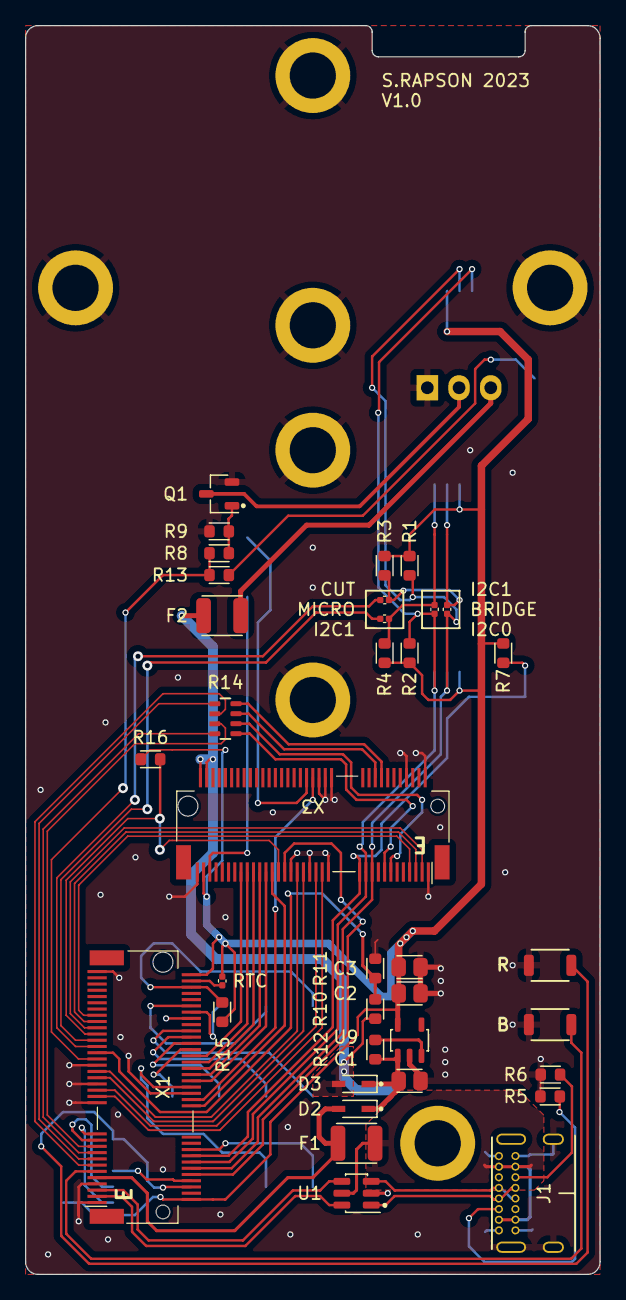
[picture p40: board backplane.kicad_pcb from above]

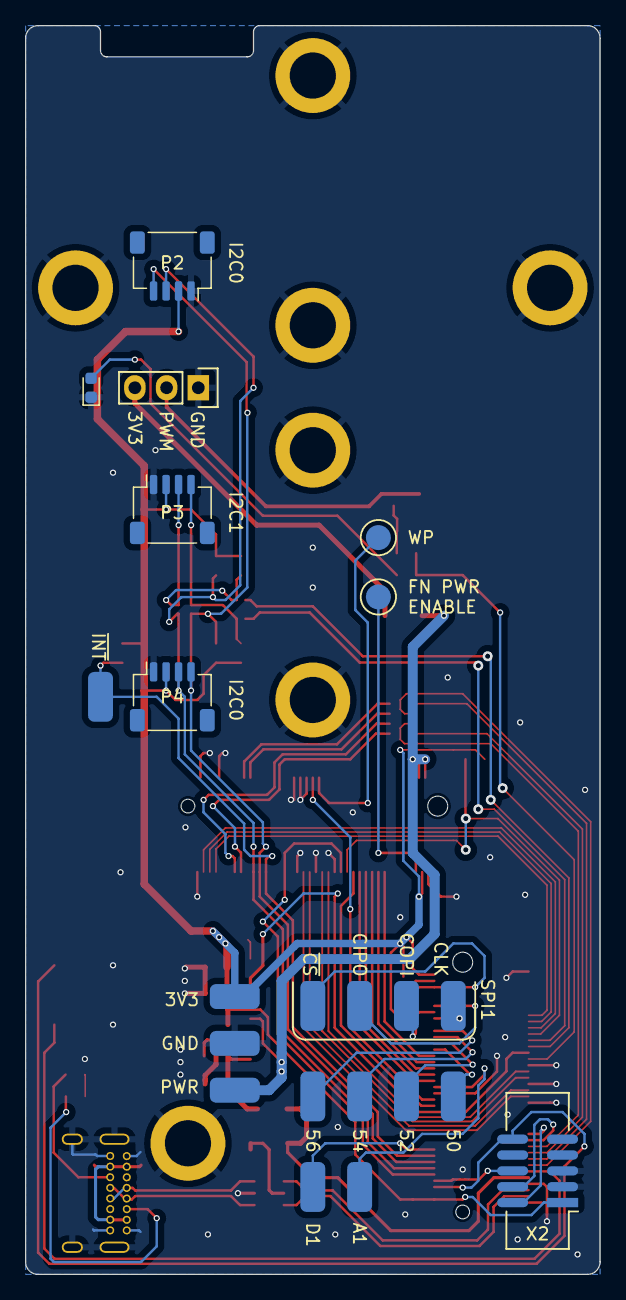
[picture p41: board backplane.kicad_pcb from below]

Board: 2 copper layers, 46.0 x 100.0 mm, 65 parts (26 on the bottom side), 68 nets.

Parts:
C1, C2, C3: 10u_X7R_2012M; CAPC2012X110N
D1: LED_YELLOW_1608M; LEDC1608X80L40N
D2, D3: 40V_500mA_SOD323; SOD2512X110N
F1, F2: 0.5A_1210L_PTC; FUSC3225X85L50N
J1: USB_C_SOCKET_RA_PTH_SIMPLE; USB_C_PTH_GCT_USB4085
MNT1, MNT2, MNT3: M2.5_SMD_2.5MM_THREADED; 9774025151R
MNT4, MNT5, MNT6, MNT7: M2.5_SMD_4.0MM_THREADED; 9774040151R
P1, P5, P6, P7, P8, P9, P11, P12, P13, P14, P15, P16, P17, P18: PAD_SOLDER_2mm
P2, P3, P4: JST_SH_4_RA; SM04B-SRSS-TB
P10: CONN_01X03; 61300311121
Q1: 2N7002P; SOT95P240X110-3L16N
R1, R2, R3, R4: 4K7_1608M; RESC1608X50N
R5, R6: 4K99_1608M; RESC1608X50N
R7, R9, R11, R12: 10K0_1608M; RESC1608X50N
R8: 10R_1608M; RESC1608X50N
R10: 20K0_1608M; RESC1608X50N
R13: 1K00_1608M; RESC1608X50N
R14: 0R_QUAD_ARRAY_1608M; R_Array_Concave_4x1608M
R15, R16: 100K_1608M; RESC1608X50N
SL1, SL4, SL5, SL6, SL7: SOLDER-LINK-2-TINY; SJ1005-2N
SW1, SW2: B3U-1000P_SPST-NO_SMD; B3U-1000P
TEST1, TEST2: PROBE_PAD; TP200
U1: USBLC6; SOT95P280X145-6L50N
U9: AP2112K-3.3; SOT95P280X145-5L30N
X1: MICROMOD_PROCESSOR_SOCKET; TE_2199230-4
X2: SWD_SMT_SOCKET; CNCTECH_3220-10-0300-00
X3: MICROMOD_FUNCTION_BOARD_SOCKET; TE_2199230-4

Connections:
+3.3V: C2.1, C3.1, P2.2, P3.2, P4.2, P15.1, R1.1, R2.1, R3.1, R4.1, R7.1, R15.1, R16.1, SL1.2, U9.5 (VOUT), X1.2 (3V3), X1.74 (3V3), X2.1 (VTref), X3.73 (3V3)
+POWER: D3.A, F2.1, P5.1, R10.1, X3.72 (VCC), X3.74 (VCC)
/Expansion IO/ANALOG_IN: P18.1, X1.38 (A1)
/Expansion IO/CIPO: P12.1, X1.64 (SPI_CIPO1/SDIO_DATA0)
/Expansion IO/CLK: P11.1, X1.60 (SPI_SCK1/SDIO_CLK)
/Expansion IO/COPI: P13.1, X1.62 (SPI_COPI1/SDIO_CMD)
/Expansion IO/DIGITAL_OUT: P17.1, X1.18 (D1/CAM_TRIG)
/Expansion IO/I2C0.SCL: P2.4, P4.4, R2.2, SL6.1, X1.14 (I2C_SCL), X3.21 (I2C_SCL)
/Expansion IO/I2C0.SDA: P2.3, P4.3, R1.2, SL7.2, X1.12 (I2C_SDA), X3.19 (I2C_SDA)
/Expansion IO/I2C1.SCL: P3.4, R4.2, SL5.1, SL6.2
/Expansion IO/I2C1.SDA: P3.3, R3.2, SL4.1, SL7.1
/Expansion IO/PWM_OUTPUT: R8.1, R13.2, X1.47 (PWM1)
/Expansion IO/~CS: P14.1, R15.2, X1.70 (~SPI_CS1/SDIO_DATA3)
/Expansion IO/~I2C_INT: P1.1, R7.2, X1.16 (~I2C_INT), X3.23 (~I2C_INT)
/Function Board/CAN.RX: X1.41 (CAN_RX), X3.41 (CAN_TX)
/Function Board/CAN.TX: X1.43 (CAN_TX), X3.43 (CAN_RX)
/Function Board/CIPO: X1.61 (SPI_CIPO), X3.7 (SPI_SDO)
/Function Board/CLK: X1.57 (SPI_SCK), X3.3 (SPI_SCK)
/Function Board/COPI: X1.59 (SPI_COPI), X3.5 (SPI_SDI)
/Function Board/CTS: R14.5, X1.15 (UARTCTS1)
/Function Board/D+: X1.35 (USBHOST_D+), X3.35 (USBHOST_D+)
/Function Board/D-: X1.37 (USBHOST_D-), X3.37 (USBHOST_D-)
/Function Board/FN_ANALOG: X1.34 (A0), X3.38 (A0)
/Function Board/FN_PWM: X1.32 (PWM0), X3.51 (F2/PWM)
/Function Board/FN_~INT: X1.10 (D0), X3.47 (F0/~INT)
/Function Board/G0: X1.40 (G0/BUS0), X3.53 (F3)
/Function Board/G1: X1.42 (G1/BUS1), X3.55 (F4)
/Function Board/G2: X1.44 (G2/BUS2), X3.57 (F5)
/Function Board/G3: X1.46 (G3/BUS3), X3.59 (F6)
/Function Board/G4: X1.48 (G4/BUS4), X3.61 (F7)
/Function Board/RTS: R14.6, X1.13 (UART_RTS1)
/Function Board/RX: R14.7, X1.19 (UART_RX1)
/Function Board/TX: R14.8, X1.17 (UART_TX1)
/Function Board/~CS: R16.2, X1.55 (~SPI_CS), X3.49 (F1/~CS)
/Power Regulation/USB_VCC: D2.A, F1.2, X1.9 (USB_VIN)
/Processor/NATIVE.D+: U1.6 (OUT_1), X1.3 (USB_D+)
/Processor/NATIVE.D-: U1.4 (OUT_2), X1.5 (USB_D-)
/Processor/SWDCLK: X1.21 (SWDCLK), X2.4 (SWCLK)
/Processor/SWDIO: X1.23 (SWDIO), X2.2 (SWDIO)
/Processor/SWO: X1.8 (G11/SWDSWO), X2.6 (SWO)
/Processor/~BOOT: SW2.1, X1.11 (BOOT)
/Processor/~RESET: SW1.1, X1.6 (~RESET), X2.10 (~RESET)
/USB Input/USBC_N: J1.A7 (D-), J1.B7 (D-), U1.3 (IN_2)
/USB Input/USBC_P: J1.A6 (D+), J1.B6 (D+), U1.1 (IN_1)
GND: C1.2, C2.2, C3.2, D1.C, J1.A1 (GND), J1.A12 (GND), J1.B1 (GND), J1.B12 (GND), J1.S1 (Shield), MNT1.1, MNT2.1, MNT3.1, MNT4.1, MNT5.1, MNT6.1, MNT7.1, P2.1, P3.1, P4.1, P10.1, P16.1, Q1.2 (S), R5.2, R6.2, R9.2, R11.2, SW1.2, SW2.2, U1.2 (GND), U9.2 (GND), X1.1 (GND), X1.7 (GND), X1.33 (GND), X1.36 (GND), X1.39 (GND), X1.45 (GND), X1.75 (GND), X2.3 (Gnd), X2.5 (Gnd), X3.1 (GND), X3.2 (GND), X3.8 (GND), X3.32 (EEPROM_A2), X3.33 (GND), X3.34 (EEPROM_A1), X3.36 (EEPROM_A0), X3.39 (GND), X3.45 (GND), X3.75 (GND)
unnamed: D1.A, R13.1
unnamed: J1.A5 (CC1), R5.1
unnamed: J1.B5 (CC2), R6.1
unnamed: P6.1, X1.56 (AUD_OUT/PCM_OUT/I2S_OUT/CAM_MCLK)
unnamed: P7.1, X1.54 (AUD_IN/PCM_IN/I2S_IN/CAM_PCLK)
unnamed: P8.1, X1.52 (AUD_LRCLK/PCM_SYNC/I2S_WS/PDM_DATA)
unnamed: P9.1, X1.50 (AUD_BCLK/PCM_CLK/I2S_SCK/PDM_CLK)
unnamed: P10.2, Q1.3 (D)
unnamed: F2.2, P10.3
unnamed: Q1.1 (G), R8.2, R9.1
unnamed: TEST1.1 (PAD), X3.71 (PWR_EN)
unnamed: TEST2.1 (PAD), X3.40 (EEPROM_WP)
unnamed: F1.1, J1.A4 (VBUS), J1.A9 (VBUS), J1.B4 (VBUS), J1.B9 (VBUS), U1.5 (VBUS)
unnamed: R12.2, U9.3 (EN)
unnamed: C1.1, D2.C, D3.C, R12.1, U9.1 (VIN)
unnamed: R10.2, R11.1, X1.49 (BATT_VIN/3)
unnamed: SL5.2, X1.53 (I2C_SCL1)
unnamed: SL4.2, X1.51 (I2C_SDA1)
unnamed: SL1.1, X1.72 (RTC_3V_BATT)
unnamed: R14.3, X3.18 (FUNC_CTS)
unnamed: R14.4, X3.16 (FUNC_RTS)
unnamed: R14.1, X3.15 (FUNC_RX)
unnamed: R14.2, X3.13 (FUNC_TX)

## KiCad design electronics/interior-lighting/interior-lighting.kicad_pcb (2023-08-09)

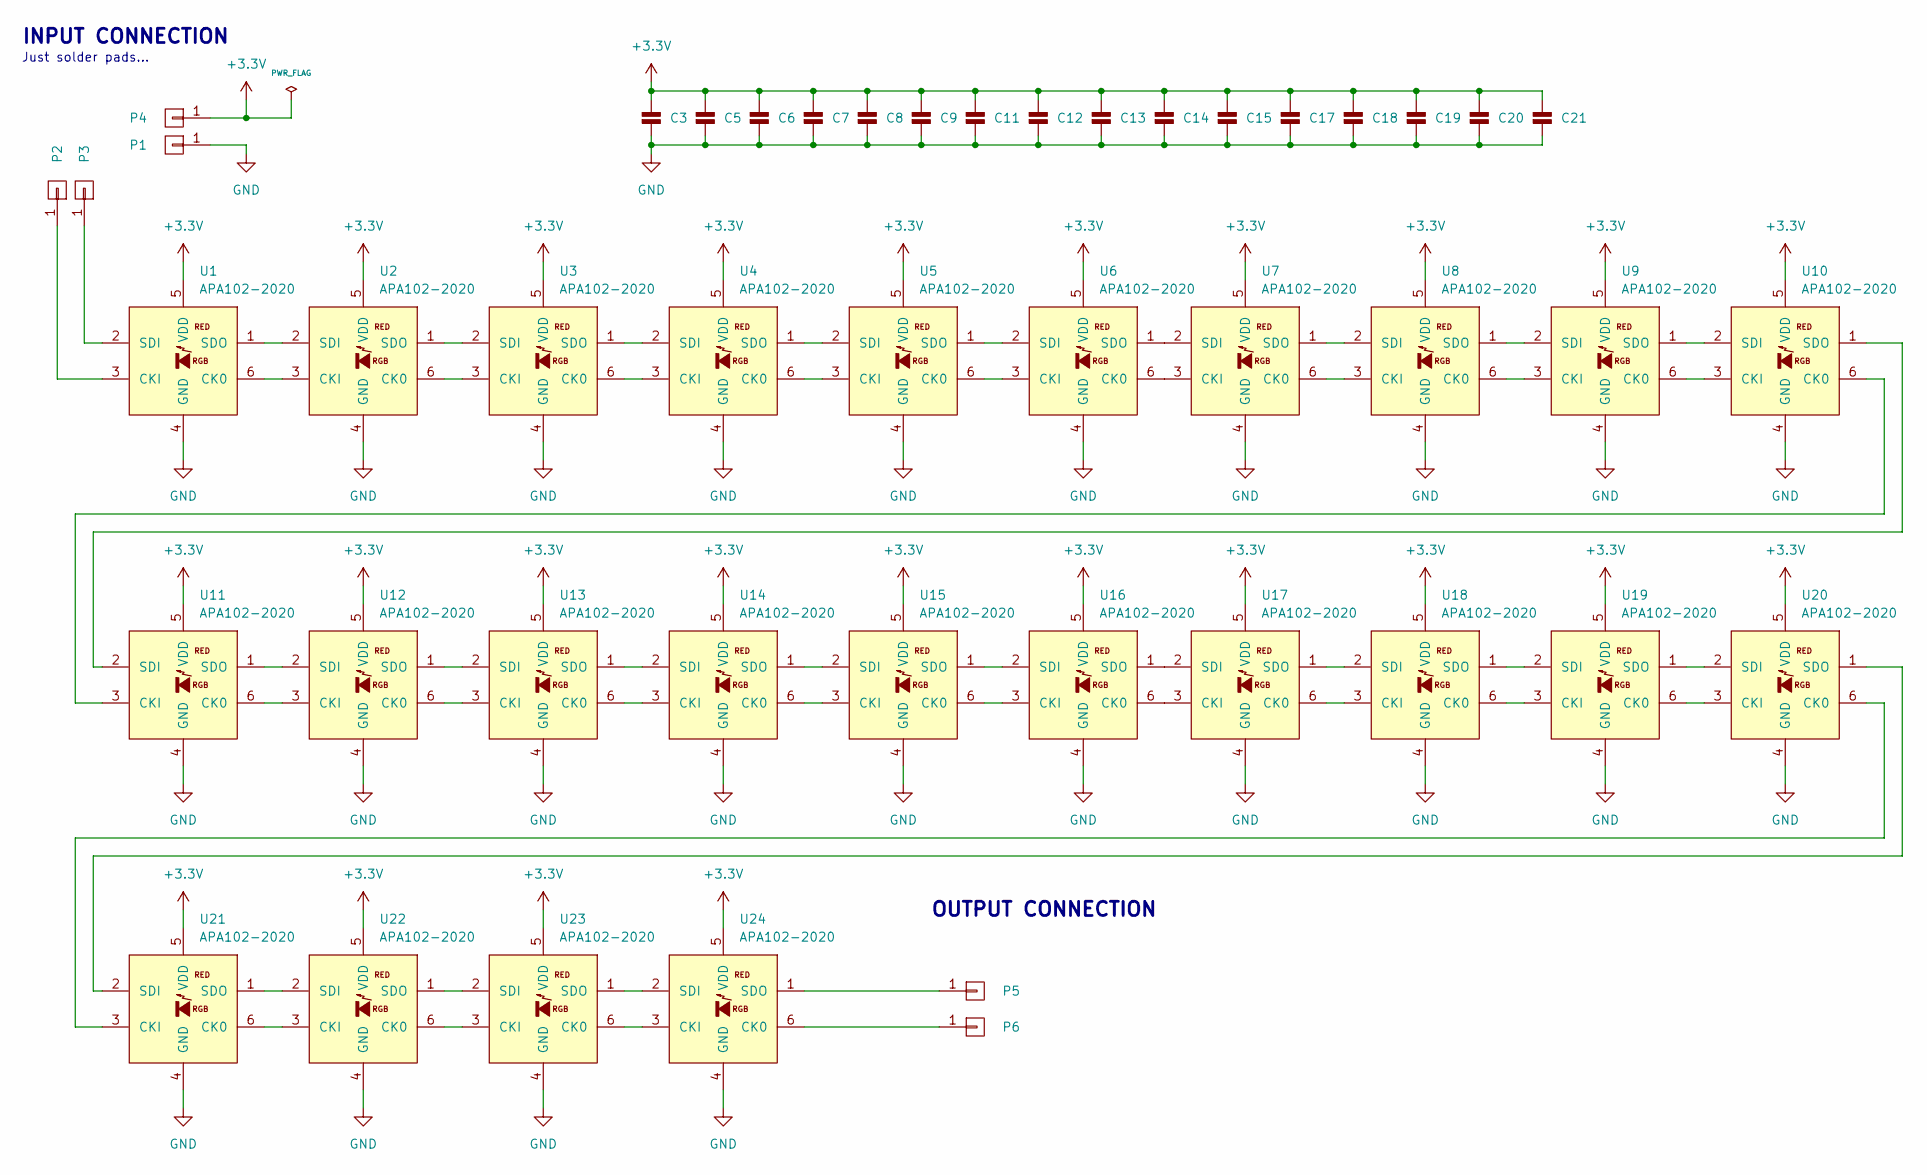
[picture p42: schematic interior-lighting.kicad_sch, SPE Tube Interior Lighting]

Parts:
C3, C5, C6, C7, C8, C9, C11, C12, C13, C14, C15, C17, C18, C19, C20, C21: 100n_X7R_1608M; CAPC1608X90L
P1, P2, P3, P4, P5, P6: PAD_SOLDER_2mm; PAD_SOLDER_2mm_SQUARE
U1, U2, U3, U4, U5, U6, U7, U8, U9, U10, U11, U12, U13, U14, U15, U16, U17, U18, U19, U20, U21, U22, U23, U24: APA102-2020; AP102_200X200X90L

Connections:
+3.3V: C3.1, C5.1, C6.1, C7.1, C8.1, C9.1, C11.1, C12.1, C13.1, C14.1, C15.1, C17.1, C18.1, C19.1, C20.1, C21.1, P4.1, U1.5 (VDD), U2.5 (VDD), U3.5 (VDD), U4.5 (VDD), U5.5 (VDD), U6.5 (VDD), U7.5 (VDD), U8.5 (VDD), U9.5 (VDD), U10.5 (VDD), U11.5 (VDD), U12.5 (VDD), U13.5 (VDD), U14.5 (VDD), U15.5 (VDD), U16.5 (VDD), U17.5 (VDD), U18.5 (VDD), U19.5 (VDD), U20.5 (VDD), U21.5 (VDD), U22.5 (VDD), U23.5 (VDD), U24.5 (VDD)
GND: C3.2, C5.2, C6.2, C7.2, C8.2, C9.2, C11.2, C12.2, C13.2, C14.2, C15.2, C17.2, C18.2, C19.2, C20.2, C21.2, P1.1, U1.4 (GND), U2.4 (GND), U3.4 (GND), U4.4 (GND), U5.4 (GND), U6.4 (GND), U7.4 (GND), U8.4 (GND), U9.4 (GND), U10.4 (GND), U11.4 (GND), U12.4 (GND), U13.4 (GND), U14.4 (GND), U15.4 (GND), U16.4 (GND), U17.4 (GND), U18.4 (GND), U19.4 (GND), U20.4 (GND), U21.4 (GND), U22.4 (GND), U23.4 (GND), U24.4 (GND)
unnamed: P2.1, U1.3 (CKI)
unnamed: P3.1, U1.2 (SDI)
unnamed: P5.1, U24.1 (SDO)
unnamed: P6.1, U24.6 (CK0)
unnamed: U1.6 (CK0), U2.3 (CKI)
unnamed: U1.1 (SDO), U2.2 (SDI)
unnamed: U2.6 (CK0), U3.3 (CKI)
unnamed: U2.1 (SDO), U3.2 (SDI)
unnamed: U3.6 (CK0), U4.3 (CKI)
unnamed: U3.1 (SDO), U4.2 (SDI)
unnamed: U4.6 (CK0), U5.3 (CKI)
unnamed: U4.1 (SDO), U5.2 (SDI)
unnamed: U5.6 (CK0), U6.3 (CKI)
unnamed: U5.1 (SDO), U6.2 (SDI)
unnamed: U6.6 (CK0), U7.3 (CKI)
unnamed: U6.1 (SDO), U7.2 (SDI)
unnamed: U7.6 (CK0), U8.3 (CKI)
unnamed: U7.1 (SDO), U8.2 (SDI)
unnamed: U8.6 (CK0), U9.3 (CKI)
unnamed: U8.1 (SDO), U9.2 (SDI)
unnamed: U10.6 (CK0), U11.3 (CKI)
unnamed: U9.6 (CK0), U10.3 (CKI)
unnamed: U9.1 (SDO), U10.2 (SDI)
unnamed: U10.1 (SDO), U11.2 (SDI)
unnamed: U11.6 (CK0), U12.3 (CKI)
unnamed: U11.1 (SDO), U12.2 (SDI)
unnamed: U12.6 (CK0), U13.3 (CKI)
unnamed: U12.1 (SDO), U13.2 (SDI)
unnamed: U13.6 (CK0), U14.3 (CKI)
unnamed: U13.1 (SDO), U14.2 (SDI)
unnamed: U14.6 (CK0), U15.3 (CKI)
unnamed: U14.1 (SDO), U15.2 (SDI)
unnamed: U15.6 (CK0), U16.3 (CKI)
unnamed: U15.1 (SDO), U16.2 (SDI)
unnamed: U16.6 (CK0), U17.3 (CKI)
unnamed: U16.1 (SDO), U17.2 (SDI)
unnamed: U17.6 (CK0), U18.3 (CKI)
unnamed: U17.1 (SDO), U18.2 (SDI)
unnamed: U18.6 (CK0), U19.3 (CKI)
unnamed: U18.1 (SDO), U19.2 (SDI)
unnamed: U19.6 (CK0), U20.3 (CKI)
unnamed: U19.1 (SDO), U20.2 (SDI)
unnamed: U20.6 (CK0), U21.3 (CKI)
unnamed: U20.1 (SDO), U21.2 (SDI)
unnamed: U21.6 (CK0), U22.3 (CKI)
unnamed: U21.1 (SDO), U22.2 (SDI)
unnamed: U22.6 (CK0), U23.3 (CKI)
unnamed: U22.1 (SDO), U23.2 (SDI)
unnamed: U23.6 (CK0), U24.3 (CKI)
unnamed: U23.1 (SDO), U24.2 (SDI)

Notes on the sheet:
OUTPUT CONNECTION
Just solder pads...
INPUT CONNECTION

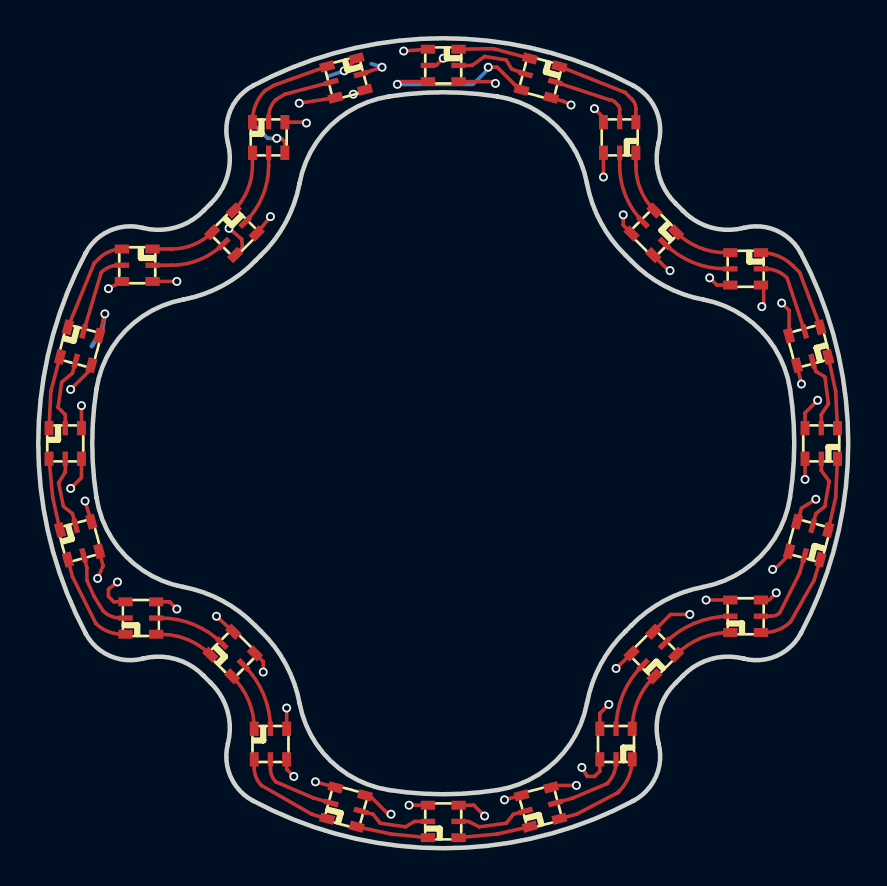
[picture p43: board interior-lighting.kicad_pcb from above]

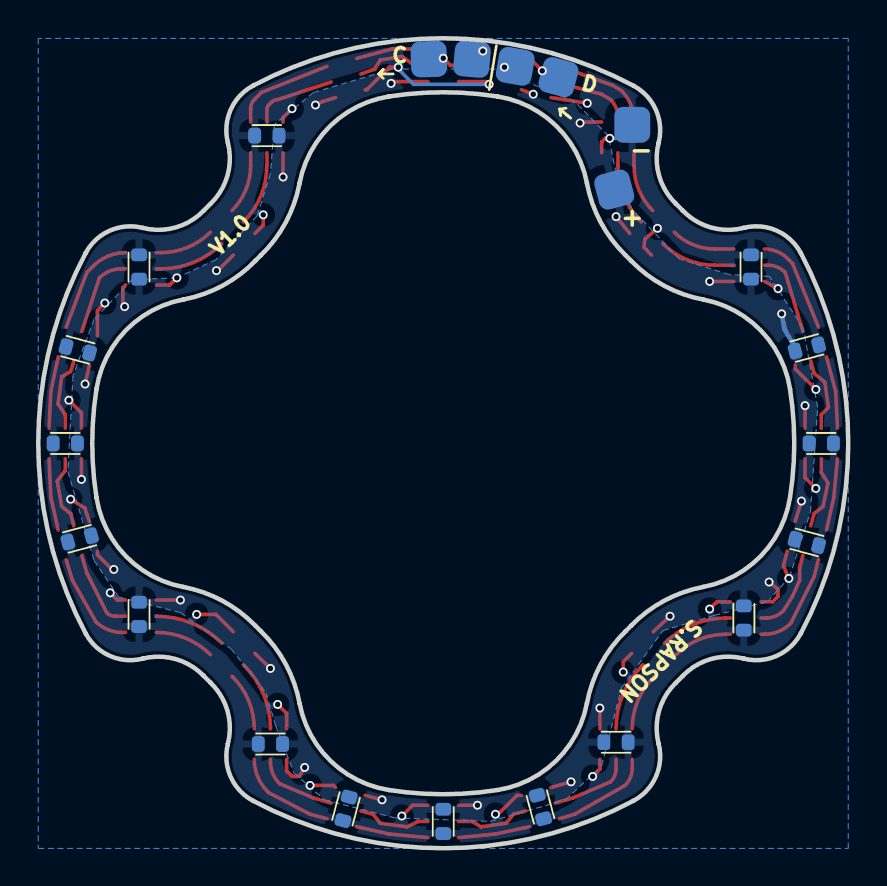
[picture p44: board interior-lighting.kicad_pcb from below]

Board: 2 copper layers, 45.0 x 45.0 mm, 46 parts (22 on the bottom side), 52 nets.

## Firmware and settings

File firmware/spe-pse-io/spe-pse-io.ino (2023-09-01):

uint32_t blink_timestamp = 0;

#define SPE_PSE_VID_DETECTION 13  // Fn board F2, MicroMod PWM0, ESP32 GPIO13
#define SPE_PSE_ENABLE_SOURCE 15  // Fn board F3, MicroMod G0, ESP32 GPIO15

#define SPE_PSE_ENABLE_OUTPUT 25  // Fn board F4, MicroMod G1, ESP32 GPIO25
#define SPE_PSE_FAULT_STATUS  17  // Fn board F6, MicroMod G3, ESP32 GPIO17
#define SPE_PSE_CURRENT_SENSE 34  // Fn board A0, MicroMod A0, ESP32 GPI34/A0

#define SPE_FN_BOARD_INT    14  // Fn board F0, MicroMod D0, ESP32 GPIO14
#define SPE_FN_BOARD_RESET  26  // Fn board F5, MicroMod G2, ESP32 GPIO26
#define SPE_FN_BOARD_CS     5   // Fn board F1, MicroMod SPI_CS, ESP32 CS0/GPIO5

#define RGB_CLK  27  // Carrier/MicroMod D1, ESP32 GPIO27
#define RGB_DATA 16   // Carrier/MicroMod RX1/AUDOUT, ESP32 GPIO16


#define PSE_CURRENT_AMPLIFIER_GAIN (100)
#define PSE_CURRENT_SHUNT_MILIOHMS (50)

#define PSE_VID_SOURCE_WARMUP_MS 7
#define PSE_VID_SOURCE_COOLDOWN_MS 5
#define PSE_VID_TEST_FILTER_COUNTS 10
#define PSE_VID_TEST_TIMEOUT_MS 200
#define PSE_VID_TIMEOUT_HOLDOFF_MS 500
#define PSE_MVFS_THRESHOLD_MA 10
#define PSE_MVFS_DURATION_MS 10

typedef enum {
  PSE_OFF = 0,
  PSE_DETECTION_FAILURE,
  PSE_DETECTION_START,
  PSE_DETECTION_WAIT,
  PSE_DETECTION_CHECK,
  PSE_DETECTION_SUCCESS,
  PSE_ON,
} PODL_DETECTION_STATES;

PODL_DETECTION_STATES pse_state = PSE_OFF;
uint32_t pse_timer;
uint8_t valid_pd_signals = 0;
bool enable_pd_power = false;

float pse_hv_current_mA( void )
{
  // Read the current amplifier
  uint16_t adc_sample = analogRead(SPE_PSE_CURRENT_SENSE);
  
  // Conversion
  float adc_voltage = (adc_sample * 3300) >> 12;
  float shunt_voltage = adc_voltage / PSE_CURRENT_AMPLIFIER_GAIN;
  float current_amps = shunt_voltage / PSE_CURRENT_SHUNT_MILIOHMS;

//  Serial.print("PSE counts: ");
//  Serial.println(adc_sample);
//  Serial.print("    adc_mv: ");
//  Serial.println(adc_voltage);
//  Serial.print("    mA: ");
//  Serial.println(current_amps/1000.0f);
  
  return current_amps/1000.0f;
}

void pse_enable_test_current( bool enable )
{
  digitalWrite( SPE_PSE_ENABLE_SOURCE, enable );
}

bool pse_check_vid_signature( void )
{
  digitalRead(SPE_PSE_VID_DETECTION);
}

void pse_enable_hv_supply( bool enable )
{
  digitalWrite( SPE_PSE_ENABLE_OUTPUT, enable );
}

bool pse_check_hv_fault( void )
{
  // Active low
  return false;//(digitalRead(SPE_PSE_FAULT_STATUS) == LOW);
}

void pse_enable_pd_power( bool active )
{
  enable_pd_power = active;
}

void pse_setup_detection_io(void)
{
    // PoDL Detection Circuit
    pinMode(SPE_PSE_VID_DETECTION, INPUT);
    pinMode(SPE_PSE_ENABLE_SOURCE, OUTPUT);

    // HV (24V) power supply switch IO
    pinMode(SPE_PSE_ENABLE_OUTPUT, OUTPUT);
    pinMode(SPE_PSE_FAULT_STATUS,  INPUT);
    pinMode(SPE_PSE_CURRENT_SENSE, INPUT);
}

// State machine to handle PoDL PSE functionality
// Should be run at >=1kHz
void pse_handle_pd()
{
  switch(pse_state)
  {
    case PSE_OFF:
      pse_enable_hv_supply( false );

      // We want to enable a potential downstream device
      if( enable_pd_power )
      {
        pse_state = PSE_DETECTION_START;
      }
    break;

    // Didn't detect a PD fast enough, etc
    case PSE_DETECTION_FAILURE:
      pse_enable_test_current( false );
      pse_enable_hv_supply( false );
      
      // Wait here for a bit before returning to OFF
      if( millis() - pse_timer >= PSE_VID_TIMEOUT_HOLDOFF_MS )
      {
        pse_timer = millis();
        pse_state = PSE_OFF;
      }
    break;
    
    // Enable the 15mA <5.6V constant current source
    case PSE_DETECTION_START:
      pse_enable_hv_supply( false );
      pse_enable_test_current( true );

      pse_timer = millis();
      pse_state = PSE_DETECTION_WAIT;
    break;

    // Wait for the test current to stabilise, downstream VID circuit to boot
    case PSE_DETECTION_WAIT:
      if( millis() - pse_timer >= PSE_VID_SOURCE_WARMUP_MS )
      {
        pse_timer = millis();
        pse_state = PSE_DETECTION_CHECK;
        valid_pd_signals = 0;
      }
    break;

    // In-spec signature voltage will be confirmed by the comparator
    case PSE_DETECTION_CHECK:
      valid_pd_signals += digitalRead(SPE_PSE_VID_DETECTION);

      // Valid PD signature voltage
      // TODO: Improve debouncing/minimum active time check
      if( valid_pd_signals >= PSE_VID_TEST_FILTER_COUNTS )
      {
        pse_timer = millis();
        pse_state = PSE_DETECTION_SUCCESS;
      }

      // Timeout handling
      if( millis() - pse_timer >= PSE_VID_TEST_TIMEOUT_MS )
      {
        pse_timer = millis();
        pse_state = PSE_DETECTION_FAILURE;
      }
    break;

    // Detected valid PD
    case PSE_DETECTION_SUCCESS:
      pse_enable_test_current( false );

      // Wait for current source to power down
      if( millis() - pse_timer >= PSE_VID_SOURCE_COOLDOWN_MS )
      {
        pse_timer = millis();
        pse_state = PSE_ON;
      }
    break;
    
    case PSE_ON:
      pse_enable_hv_supply( true );

      // Part of the maintain full-voltage signature requires the PD to 
      // draw a minimum current (typically 10mA, but lower is allowed?) every 10ms
      // Lower power devices are meant to pulse their load to achieve this
//      if( pse_hv_current_mA() >= PSE_MVFS_THRESHOLD_MA )
//      {
//        // Reset the timer
//        pse_timer = millis();
//      }
//
//      if( millis() - pse_timer >= PSE_MVFS_DURATION_MS )
//      {
//        pse_timer = millis();
//        pse_state = PSE_DETECTION_FAILURE;
//      }
      
      // Check for faults or user wanting to disable power
      if( pse_check_hv_fault() || !enable_pd_power )
      {
        pse_timer = millis();
        pse_state = PSE_DETECTION_FAILURE;
      }
    break;
    
    default:
      // ???
      pse_state = PSE_DETECTION_FAILURE;
    break;
  }
  
}



void setup()
{
    Serial.begin(115200);
    Serial.println("MicroMod SPE PoDL PSE Fn Board");
    Serial.println("PD Detection and powerup demo");

    pinMode(LED_BUILTIN, OUTPUT);

    pse_setup_detection_io();

    // ADIN1110 IO
    pinMode(SPE_FN_BOARD_INT, INPUT);
//    attachInterrupt(digitalPinToInterrupt(SPE_FN_BOARD_INT), some_fn, CHANGE);
    pinMode(SPE_FN_BOARD_RESET, OUTPUT);
    pinMode(SPE_FN_BOARD_CS, OUTPUT);

}

void loop()
{
    pse_hv_current_mA();
    
    pse_handle_pd();
   
    if( millis() - blink_timestamp >= 250 )
    {
        bool state = !digitalRead(LED_BUILTIN);
        digitalWrite(LED_BUILTIN, state ); 
        blink_timestamp = millis();

        if( millis() >= 5000 )
        {
            // Attempt to power the downstream device
            pse_enable_pd_power( true );
        }
    }
    
    delayMicroseconds(100);
}

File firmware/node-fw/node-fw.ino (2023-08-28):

uint32_t led_pwm_timestamp = 0;
uint32_t led_rgb_timestamp = 0;


void setup()
{
    led_pwm_setup();
    led_rgb_setup();

    led_pwm_timestamp = millis();
    led_rgb_timestamp = millis();
}

void loop()
{
    if( millis() - led_rgb_timestamp >= 20 )
    {
        led_pwm_loop();
    }
 
    if( millis() - led_rgb_timestamp >= 10 )
    {
        led_rgb_loop();
    }
  

}

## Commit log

2023-07-26 First pass waterproofed tube concept
    [BALLAST-200G-R2.SLDPRT, BAR02-ASM-R2-PUBLIC.SLDPRT, INDICATOR-M10-X-R2-PUBLIC.SLDPRT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]
2023-07-26 Rough buoyancy calcs
    Attempt to work out positive or negative buoyancy, weight budget.
    [tube-buoyancy-calcs.ods]
2023-08-01 Rough interior lighting ring PCB
    [interior-lighting.kicad_pcb, interior-lighting.kicad_sch]
2023-08-04 Start stubbing out backplane PCB
    [backplane.kicad_pcb, backplane.kicad_sch]
2023-08-05 Rough cad models for Sparkfun modules/boards
    Used for layout reference
    [function-board-stub.SLDPRT, micro-mod-stub.SLDPRT, sf-qwiic-sensor.SLDPRT]
2023-08-05 Tube 2D drawing
    For size/positioning reference
    [tube-assembly.SLDDRW]
2023-08-05 Adds PDF for 2D tube drawing
2023-08-06 Backplane schematic capture and PCB shape
    [backplane.kicad_pcb, backplane.kicad_sch, function-board.kicad_sch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]
2023-08-06 Continue backplane PCB
    [backplane.kicad_pcb, backplane.kicad_sch, function-board.kicad_sch]
2023-08-07 Continue backplane
    [backplane.kicad_pcb, backplane.kicad_sch, function-board.kicad_sch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]
2023-08-08 Continue schematic tweaks, start routing backplane
    [backplane.kicad_pcb, backplane.kicad_sch, expansion.kicad_sch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]
2023-08-08 Continue backplane design Cleanup schematic, most routing and placement done
    [backplane.kicad_pcb, backplane.kicad_sch, expansion.kicad_sch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]
2023-08-08 Continued routing Labels, most traces, most pours
    [backplane.kicad_pcb, expansion.kicad_sch]
2023-08-09 Backplane routing complete General schematic cleanup, board cosmetics etc
    [backplane.kicad_pcb, backplane.kicad_sch, expansion.kicad_sch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]
2023-08-09 Backplane V1.0 gerbers and schematic export
    [backplane-B_Cu.gbr, backplane-B_Mask.gbr, backplane-B_Paste.gbr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]
2023-08-09 Internal lighting board finished
    [interior-lighting.kicad_pcb, interior-lighting.kicad_sch]
2023-08-09 Add KiCAD gitignore entries
    [interior-lighting-B_Cu.gbr, interior-lighting-B_Mask.gbr, interior-lighting-B_Paste.gbr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]
2023-08-10 Started PD detection ID circuit
    [MCP65R41T-hysteresis-calc.ods, atl321-shunt-regulator-calc.ods, spe-sink.kicad_pcb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]
2023-08-11 Fixed backplane i2c connector 3D model/footprint linkage Also minor schematic cleanup
    [backplane.kicad_pcb, backplane.kicad_sch, expansion.kicad_sch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]
2023-08-11 Continue work on PD function board schematic
    [spe-sink.kicad_sch]
2023-08-12 Add MAC+PHY, other parts to PD function board sch
    [ethernet.kicad_sch, micromod.kicad_sch, podl-pd.kicad_sch.kicad_sch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]
2023-08-12 Building out PDoE filter/isolation, etc
    [ethernet.kicad_sch, power.kicad_sch, spe-sink.kicad_sch]
2023-08-13 Printable mounting clamp, small spacer to stop tube rolling off desk
    [bulkhead-internal-mast.SLDPRT, clamp-strap-lower.SLDPRT, clamp-strap-upper.SLDPRT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]
2023-08-13 Printable PCB mounting brackets, LED ring diffuser
    [cable-tidy.SLDPRT, led-diffuser.SLDPRT, mounting-spine-lower.SLDPRT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]
2023-08-13 Drawing/detail of PCB vertical component clearances
    Needed to know if large PDoE inductors can fit in the tube
2023-08-14 Add basic renders of PCBs
2023-08-14 PCB schematic PDFs in git for easy access
    [flange-led-ring.DXF]
2023-08-14 PD function board schematic progress
    [ethernet.kicad_sch, micromod.kicad_sch, podl-pd.kicad_sch.kicad_sch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]
2023-08-15 PD function board bulk regulator, cleanup, part placement
    [INA180-resistor-calc.ods, ethernet.kicad_sch, micromod.kicad_sch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]
2023-08-16 PD sink board routing, minor sch changes, etc
    [ethernet.kicad_sch, micromod.kicad_sch, podl-pd.kicad_sch.kicad_sch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]
2023-08-16 PD sink PCB design 'finished', page cleanup, etc
    [ethernet.kicad_sch, micromod.kicad_sch, podl-pd.kicad_sch.kicad_sch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]
2023-08-16 Start PSE schematic, detection source/validation circuit, etc
    [ethernet.kicad_sch, micromod.kicad_sch, podl-pse.kicad_sch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]
2023-08-16 Fix current amplifier part choice on PD board
    [power.kicad_sch, spe-sink.kicad_pcb]
2023-08-16 PSE part placement, partial routing
    [podl-pse.kicad_sch, spe-source.kicad_pcb, spe-source.kicad_sch]
2023-08-16 PSE routing spaghetti complete
    [micromod.kicad_sch, podl-pse.kicad_sch, power.kicad_sch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]
2023-08-17 TLV6700 window comparator calculator spreadsheet, PCB export settings
    [TVL6700-window-comparator-calc.ods, spe-sink.kicad_pcb, spe-source.kicad_pcb]
2023-08-17 V1.0 gerbers for PoDL PSE and PD boards
    [spe-sink-B_Cu.gbr, spe-sink-B_Mask.gbr, spe-sink-B_Paste.gbr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]
2023-08-17 Schematic PDFs for PSE and PD function boards
2023-08-19 Revised PSE input voltage limit resistor values
    [podl-pd.kicad_sch.kicad_sch, power.kicad_sch]
2023-08-19 PCB models imported, test assembly
    [M2.5x4-pan-head.sldprt, flange-led-ring.DXF, flange-led-ring.SLDPRT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]
2023-08-19 STL exports for internal mounting braces
    [led-diffuser-2mm-thick.STL, led-diffuser.STL, mounting-spine-lower.STL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]
2023-08-19 Update assembly files with high detail PCB assembly
2023-08-21 Sensor bringup/test sketches
2023-08-25 Additional docs
    [TPS26625-calc.xlsm, shopping-list.ods]
2023-08-26 PSE firmware to manage PD detection and powerup
2023-08-27 Minor tweaks to test firmware, LED test sketch
2023-08-28 Minor tweaks to test sketches
    [podl-pse.kicad_sch, power.kicad_sch]
2023-09-02 Random uncommitted KiCAD tweaks
    [podl-pse.kicad_sch, spe-sink.kicad_sch, spe-source.kicad_sch]
